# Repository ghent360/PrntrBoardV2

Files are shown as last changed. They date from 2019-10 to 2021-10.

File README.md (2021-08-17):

PrntrBoard V2
======================
PrntrBoard V2 is the next iteration of my 3D printer controller design. The V1 was very good, except it had one major drawback - the stepper drivers were soldered on the board which would make the design expensive.
This V2 design has 6 replaceable motor drivers. While traditional RAMPS based boards use pin headers to house the driver boards, I'm using PCIe 1x slots. This design has several advantages:
  + the driver PCB layout can be more flexible as there are fewer constraints on the driver board dimensions
  + drivers are placed vertically on the board which allows for more efficient space utilization as well as more efficient cooling
  + PCIe 1x slots have 36 pins which allows for greater design flexibility

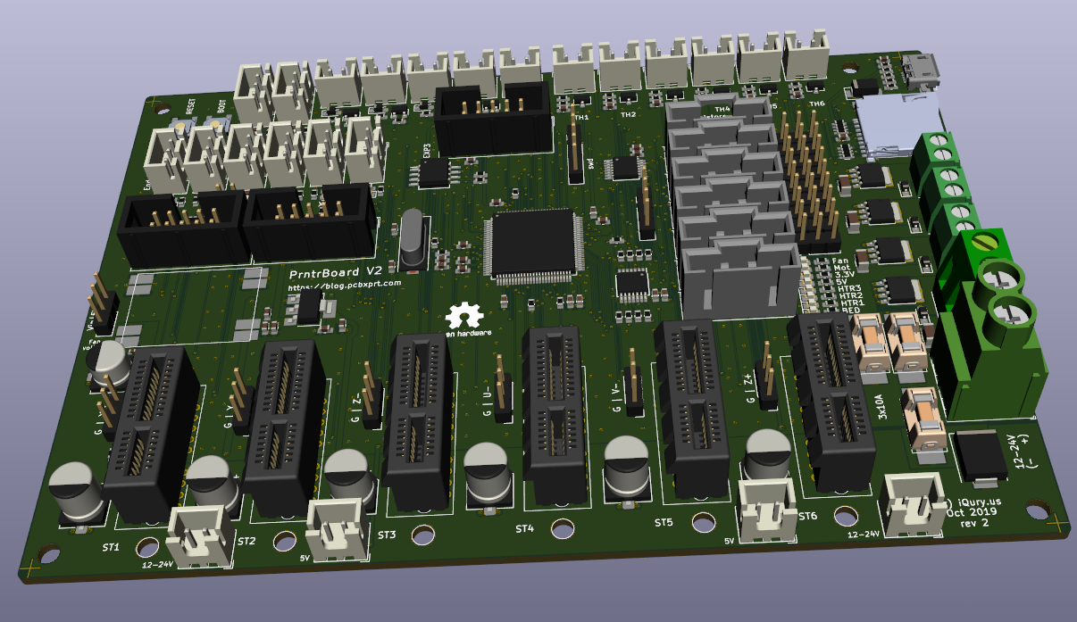
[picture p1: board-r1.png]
Picture of rev-1 KiCad Rendering


Project Status
-----
The following functionality has been verified on the rev1 prototype board with Marlin firmware:
  + TMC2660 and TMC2209 drivers working and able to move motors
  + Endstops
  + Heaters and thermistor inputs
  + LCD interface with 12864 panel from FYSETC and REPRAP Discount Graphics Panel.
  + Micro SD-card interface
  + EEPROM
  + Fan control

Features of the board:
-----
  + up to 6x replaceable stepper motor drivers
  + 32-bit Arm processor with floating point support running at 168MHz (STM32F407)
  + up to 6 thermistors or 6 thermocouples for temperature control
  + 4 power heaters (1 bed and up to 3 extruder heaters) with PWM power control
  + 5 low power PWM connectors with selectable voltage (5V vs 12-24V) for fans or LEDs
  + 8 end stops with option to use stall detection from the stepper drivers on 6 of them
  + micro-sd card support with SDIO for fast file transfer
  + 2 extra serial ports for WiFi and or smart LCD screen control
  + RAMPS LCD screen support
  + Marlin 2.0 firmware or Smoothieware V1.0, RRF port in progress, Klipper port in progress.
  + 4 extra fan connectors (2x5V and 2x12-24V)
  + Input voltage: 12-24V
  + CAN bus connector contributed by ArkadiuszRaj.

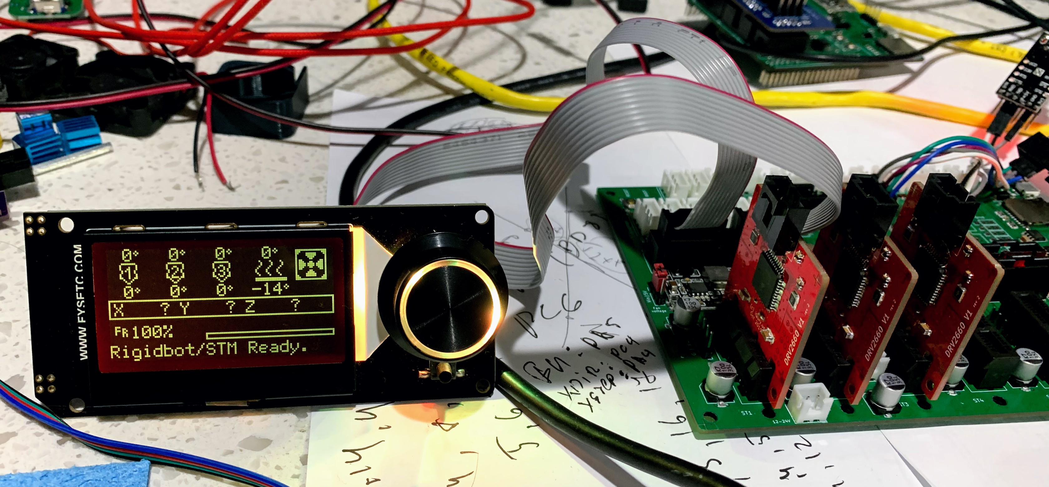
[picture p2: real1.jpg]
Picture of rev-1 prototype


Drivers
------
High power driver using Trinamic TMC2660. Should support up to 2.5A RMS current per phase with forced cooling. Supports stall detection. Driver current is adjustable via SPI.

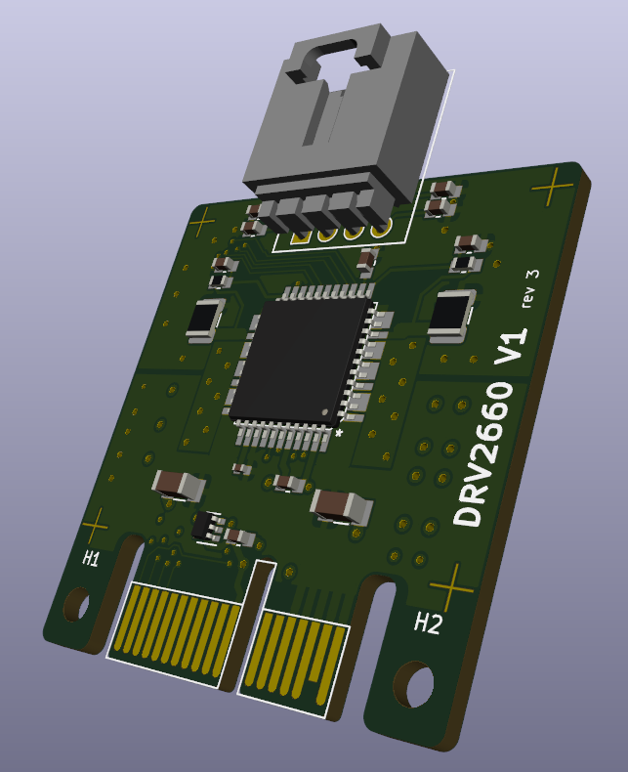
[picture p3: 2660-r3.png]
KiCad rendering of the 2660 driver board
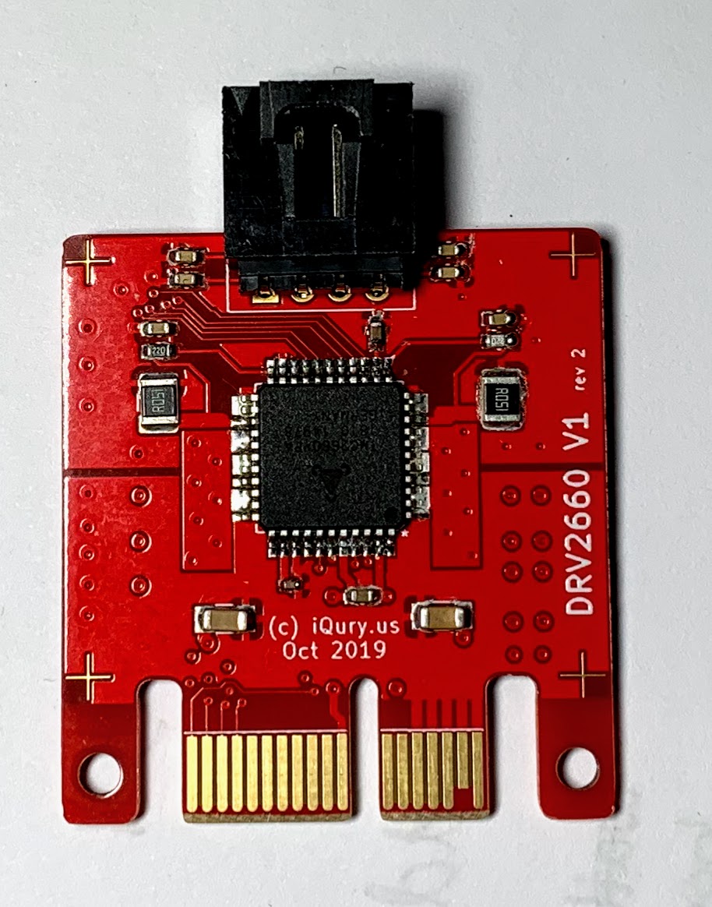
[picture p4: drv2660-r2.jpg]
2660 r2 driver board
 

Versatile "economy" driver using Trinamic TMC2209. Should support up to 1.8A RMS current per phase with forced cooling. Supports stall detection. Driver current is adjustable via UART.

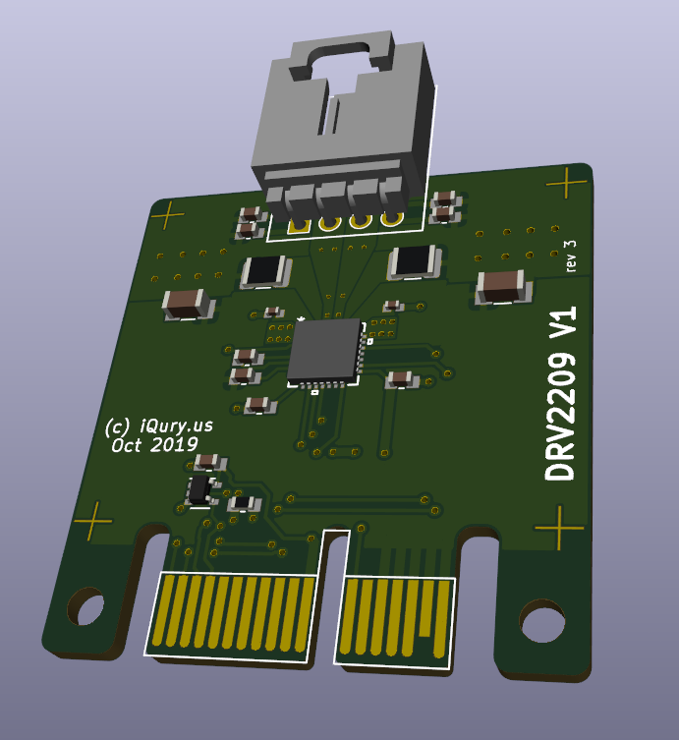
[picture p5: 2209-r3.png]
KiCad rendering of the 2209 driver board
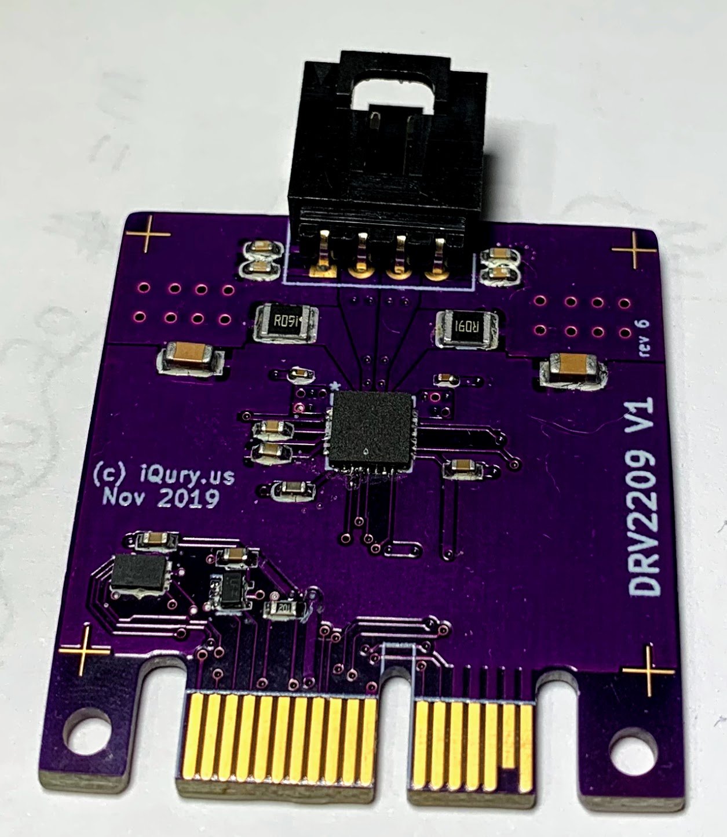
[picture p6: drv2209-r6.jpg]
2209 r6 driver board


High voltage driver (up to 42V) using Trinamic TMC2130. Should support up to 1.1A RMS current per phase with forced cooling. Supports stall detection. Driver current is adjustable via SPI. The driver board has separate power terminal.

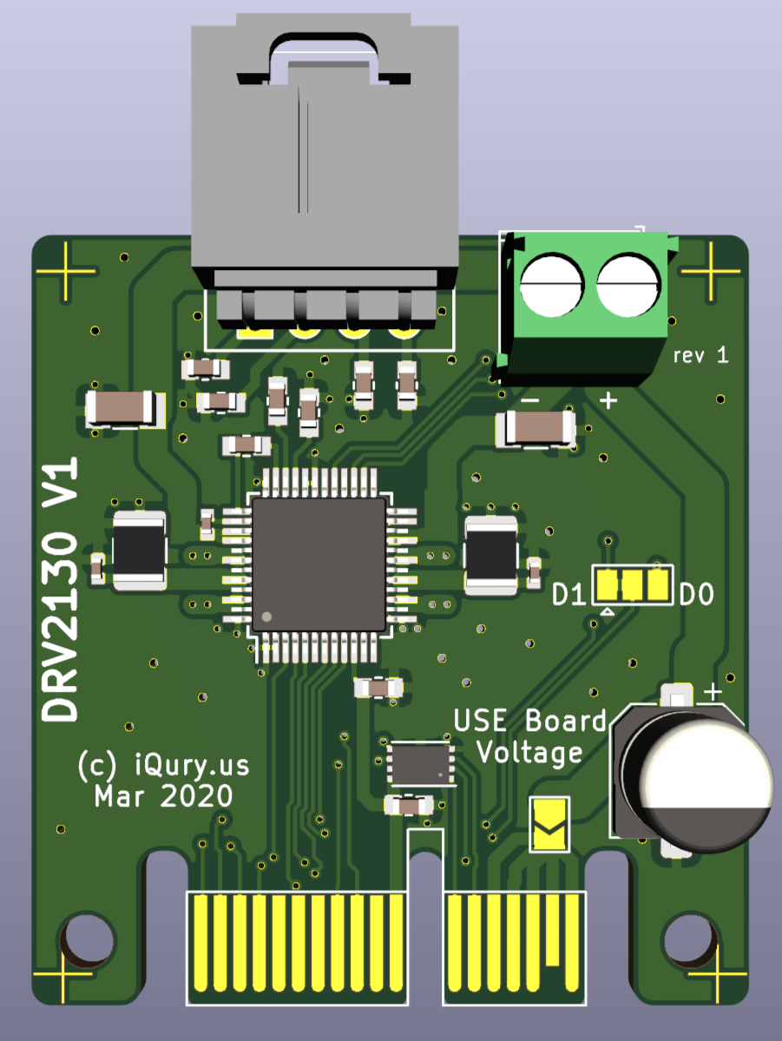
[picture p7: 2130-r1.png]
KiCad rendering of the 2130 driver board


Very high current driver design using TMC5161 and TMC2160 with external MOSFETS are also possible. In addition an adapter board for Pololu style stepper drivers is planned for backwards compatibility with old drivers.

Software
------

Marlin v2 is working on the board. I have a port of Smoothieware V1. Klipper is functional with some [fixes] (https://github.com/ghent360/klipper). RepRepFirmware ports is in early stages and not yet functional.

Visit [my blog](https://blog.pcbxprt.com/) for status updates on the development of the board.

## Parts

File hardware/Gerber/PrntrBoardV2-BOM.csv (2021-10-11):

Comment | Designator | Footprint | LCSC | LCSC Part # | Part #
10uF | C20,C23,C26,C56,C2,C5,C6,C15 | PrntrBoardV2:C_0603_1608Metric |  | C19702 | CL10A106KP8NNNC
0.1uF | C21,C22,C57,C18,C19,C54,C1,C4,C7,C8,C9,C10,C11,C12,C13,C14,C17,C53,C46 | PrntrBoardV2:C_0603_1608Metric |  | C14663 | CC0603KRX7R9BB104
0.1uF 50V | C24 | PrntrBoardV2:C_0603_1608Metric |  | C14663 | CL05B104KO5NNNCC0603KRX7R9BB104C
100uF 35V | C25,C47,C48,C49,C50,C51,C52 | Capacitor_SMD:CP_Elec_6.3x7.7 |  | C134792 | VES101M1VTR-0607
1000pF | C27,C28,C29,C30,C31,C32,C33,C34,C35,C36,C37,C38,C39,C40,C3,C16,C45 | PrntrBoardV2:C_0603_1608Metric |  | C1588 | CL10B102KB8NNNC
10uF 50V | C41,C42,C43,C44 | PrntrBoardV2:C_1206_3216Metric |  | C13585 | CL31A106KBHNNNE
B5819W | D1,D21,D22,D25,D26,D27,D29,D30,D31,D33 | Diode_SMD:D_SOD-123 |  | C8598 | B5819W
LED | D2,D3,D4,D5,D13,D14,D15,D16,D17,D18,D19,D20,D23,D24,D28,D32 | PrntrBoardV2:LED_0603_1608Metric |  | C2286 | KT-0603R
10V | D6 | Diode_SMD:D_SOD-323 |  | C131828 | LM3Z10VT1G
BAT54S | D7,D8,D9,D10,D11,D12 | Package_TO_SOT_SMD:SOT-23 |  | C181201 | BAT54S
IDC 2x5 | EXP1,EXP2,EXP3 | Connector_IDC:IDC-Header_2x05_P2.54mm_Vertical |  | C5661
500mA | F1 | PrntrBoardV2:R_0603_1608Metric |  | C261937 | TLC-FSMD050
Fuse | F2,F3,F4 | PrntrBoardV2:2410_FuseFolder
600 ohm @ 100MHz | FB1 | Inductor_SMD:L_0805_2012Metric |  | C1017 | GZ2012D601TF
JST XH | J1,J2,J22,J23,J24,J25,J26,J27,J_TH1,J_TH2,J_TH3,J_TH4,J_TH5,J_TH6,J4,J16,J18,J19,J21 | Connector_JST:JST_XH_B2B-XH-A_1x02_P2.50mm_Vertical
KF350 | J28,J6,J17,J20 | PrntrBoardV2:TerminalBlock_Phoenix_PT-1,5-2-3.5-H_1x02_P3.50mm_Horizontal
RJ12_Shielded | J29 | Connector_RJ:RJ12_Amphenol_54601
USB_B_Micro | J3 | PrntrBoardV2:MC-101C |  | C183609 | SOFNG MC-101C
KF129 | J5 | PrntrBoardV2:TerminalBlock_Phoenix_MKDS-1,5-2-5.08_1x02_P5.08mm_Horizontal
Conn_01x03_Male | J7,J8,J9,J10,J11,J12,J13,J14,J15 | Connector_PinHeader_2.54mm:PinHeader_1x03_P2.54mm_Vertical
Jumper_2_Open | JP1 | Connector_PinHeader_2.54mm:PinHeader_1x02_P2.54mm_Vertical |  | C160332
Jumper_3_Open | JP2,JP3,JP4,JP5,JP6,JP7,JP8 | Connector_PinHeader_2.54mm:PinHeader_1x03_P2.54mm_Vertical |  | C152153
Serial 0 | J_SER1 | Connector_PinHeader_2.54mm:PinHeader_1x04_P2.54mm_Vertical |  | C358686
PCIe_Stepper | J_ST1,J_ST2,J_ST3,J_ST4,J_ST5,J_ST6 | PrntrBoardV2:AMPHENOL_10018784-10210TLF
SWD | J_SWD1 | Connector_PinHeader_2.54mm:PinHeader_1x05_P2.54mm_Vertical
JST XH 3p | J_U-1,J_V-1,J_X+1,J_X-1,J_Y+1,J_Y-1,J_Z+1,J_Z-1 | Connector_JST:JST_XH_B3B-XH-A_1x03_P2.50mm_Vertical
KF635 | J_power_in1 | TerminalBlock_MetzConnect:TerminalBlock_MetzConnect_Type701_RT11L02HGLU_1x02_P6.35mm_Horizontal
Net-Tie_2 | NT1 | NetTie:NetTie-2_SMD_Pad0.5mm
NCE40P40K | Q1 | Package_TO_SOT_SMD:TO-252-2 |  | C130100 | NCE40P40K
22 | R10,R11,R72 | PrntrBoardV2:R_0603_1608Metric |  | C23345 | 0603WAF220JT5E
10k | R13,R14,R19,R20,R23,R24,R27,R28,R2,R73,R77,R78,R32,R33,R34,R38,R39,R40,R43,R44,R47,R1,R3,R5,R6,R7,R70,R48,R49,R50,R54,R55,R56,R58,R60,R61,R63,R64,R67,R68 | PrntrBoardV2:R_0603_1608Metric |  | C25804 | 0603WAF1002T5E
470 | R15,R45,R46 | PrntrBoardV2:R_0603_1608Metric |  | C23179 | 0603WAF4700T5E
1k | R16,R29,R30,R31,R35,R36,R37,R41,R42,R8,R51,R57,R62,R65,R69 | PrntrBoardV2:R_0603_1608Metric |  | C21190 | 0603WAF1001T5E
4k7 | R17,R18,R21,R22,R25,R26 | PrntrBoardV2:R_0603_1608Metric |  | C23162 | 0603WAF4701T5E
180 | R52,R53,R59,R66 | PrntrBoardV2:R_0603_1608Metric |  | C22828 | 0603WAF1800T5E
100k | R71,R12 | PrntrBoardV2:R_0603_1608Metric |  | C25803 | 0603WAF1003T5E
56 | R74,R75 | PrntrBoardV2:R_0603_1608Metric |  | C25196 | 0603WAF560JT5E
1.5k | R9 | PrntrBoardV2:R_0603_1608Metric |  | C22843 | 0603WAF1501T5E
4x470 | RN1,RN2 | Resistor_SMD:R_Array_Convex_4x0603 |  | C25510 | 4D03WGJ0471T5E
4x10k | RN3 | Resistor_SMD:R_Array_Convex_4x0603 |  | C29718 | 4D03WGJ0103T5E
SW_Push | SW_BOOT1,SW_RST1 | PrntrBoardV2:Button_4x4 |  | C318884 | TS-1187A-B-A-B
TC | TC1,TC2,TC3,TC4,TC5,TC6 | kicad-molex-sl-footprints:Molex-SL-6POS
SI2318CDS | TR1,TR4,TR6,TR7,TR9 | PrntrBoardV2:SOT-23 |  | C20917 | AO3400A
PSMN7R0-30YL | TR2,TR3,TR5,TR8 | PrntrBoardV2:SOT-669_LFPAK |  | C427523 | PSMN1R5-30YLC
74LVC125 | U1,U7 | Package_SO:TSSOP-14_4.4x5mm_P0.65mm |  | C6059 | 74LVC125APW,118
STM32F407VETx | U2 | Package_QFP:LQFP-100_14x14mm_P0.5mm |  | C28730 | STM32F407VET6
24LC64 | U3 | Package_SO:SO-8_3.9x4.9mm_P1.27mm |  | C5460 | 24LC64T-I/SN
AMS1117-3.3 | U4 | Package_TO_SOT_SMD:SOT-223-3_TabPin2 |  | C6186 | AMS1117-3.3
74HCT04 | U6 | Package_SO:TSSOP-14_4.4x5mm_P0.65mm |  | C131317 | 74HCT04PW,118
TJA1040 | U8 | Package_SO:SOIC-8_3.9x4.9mm_P1.27mm |  | C6951 | TJA1040T/CM,118
12MHz | X1 | Oscillator:Oscillator_SMD_EuroQuartz_XO32-4Pin_3.2x2.5mm |  | C29752 | SIT1602AI-22-33E-12.000000D
MicroSD | XS1 | PrntrBoardV2:Conn_uSDcard |  | C111196 | SOFNG TF-15×15

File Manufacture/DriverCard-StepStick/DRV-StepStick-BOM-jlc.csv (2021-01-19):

Comment | Designator | Footprint | LCSC | LCSC Part # | Part #
0.1uF | C3 | PrntrBoardV2:C_0603_1608Metric |  | C14663 | CC0603KRX7R9BB104
100uF 35V | C4 | Capacitor_SMD:CP_Elec_6.3x7.7 |  | C134792 | VES101M1VTR-0607
PCIe_Stepper | J1 | Connector_PCBEdge:BUS_PCIexpress
Motor | J2 | PrntrBoardV2:Molex-SL-4POS
StepStickL | J3 | Connector_PinSocket_2.54mm:PinSocket_1x08_P2.54mm_Vertical
StepStickR | J4 | Connector_PinSocket_2.54mm:PinSocket_1x08_P2.54mm_Vertical
Conn_01x04 | J5 | Connector_PinHeader_2.54mm:PinHeader_1x04_P2.54mm_Vertical
SPI Mode | J6 | Connector_PinHeader_2.54mm:PinHeader_2x04_P2.54mm_Vertical
Conn_01x02 | J7 | Connector_PinSocket_2.54mm:PinSocket_1x02_P2.54mm_Vertical
Clock/Sleep | JP3 | Connector_PinHeader_2.54mm:PinHeader_1x03_P2.54mm_Vertical
Reset | JP4 | Connector_PinHeader_2.54mm:PinHeader_1x03_P2.54mm_Vertical
10k | R1,R2 | Resistor_SMD:R_0603_1608Metric |  | C29718 | 4D03WGJ0103T5E
74LVC1G06 | U2 | Package_TO_SOT_SMD:SOT-353_SC-70-5 |  | C7828 | SN74LVC1G06DCKR

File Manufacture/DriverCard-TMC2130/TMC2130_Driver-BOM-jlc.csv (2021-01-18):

Comment | Designator | Footprint | LCSC | LCSC Part # | Part #
0.1uF | C1,C6,C16,C17 | PrntrBoardV2:C_0603_1608Metric |  | C14663 | CC0603KRX7R9BB104
1000pF | C11,C12,C13,C14 | PrntrBoardV2:C_0603_1608Metric |  | C1588 | CL10B102KB8NNNC
10uF 50V | C2,C4 | PrntrBoardV2:C_1206_3216Metric |  | C13585 | CL31A106KBHNNNE
0.022uF 50V | C3 | PrntrBoardV2:C_0603_1608Metric |  | C21122 | CL10B223KB8NNNC
100uV 35V | C5 | Capacitor_SMD:CP_Elec_6.3x7.7 |  | C171732 | VE-101M1VTR-0607
4.7uF | C7 | PrntrBoardV2:C_0603_1608Metric |  | C19666 | CL10A475KO8NNNC
0.47uF | C8 | Capacitor_SMD:C_0603_1608Metric |  | C1623 | CL10B474KA8NNNC
0.1uF 50V | C9,C10,C15 | PrntrBoardV2:C_0402_1005Metric |  | C1525 | CL05B104KO5NNNC
SBRT5A50SA | D1 | Diode_SMD:D_SMA |  | C264107 | SBRT5A50SA-13
3A | F1 | Fuse:Fuse_1206_3216Metric |  | C208499 | SF-1206F300-2
PCIe_Stepper | J1 | Connector_PCBEdge:BUS_PCIexpress
Conn_01x04_Male | J2 | PrntrBoardV2:Molex-SL-4POS
Screw_Terminal_01x02 | J3 | TerminalBlock_Phoenix:TerminalBlock_Phoenix_PT-1,5-2-3.5-H_1x02_P3.50mm_Horizontal
DIAG_Sel | JP1 | Jumper:SolderJumper-3_P1.3mm_Bridged12_Pad1.0x1.5mm
Use VM | JP2 | Jumper:SolderJumper-2_P1.3mm_Open_TrianglePad1.0x1.5mm
0R12 | R1,R2 | Resistor_SMD:R_2512_6332Metric |  | C81248 | 25121WF120LT4E
TMC2130 | U1 | PrntrBoardV2:tmc5130-nc |  | C328952 | TMC2130A-TA
24LC02 | U2 | PrntrBoardV2:TDFN-8-1EP_3x2mm_P0.5mm_EP1.56x1.45mm |  | C184154 | CAT24C02VP2IGT3A

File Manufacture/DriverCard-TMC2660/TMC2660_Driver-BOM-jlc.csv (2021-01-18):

Comment | Designator | Footprint | LCSC | LCSC Part # | Part #
10uF 50V | C1,C2 | PrntrBoardV2:C_1206_3216Metric |  | C13585 | CL31A106KBHNNNE
100uF 35V | C13 | Capacitor_SMD:CP_Elec_6.3x7.7 |  | C171732 | VE-101M1VTR-0607
0.1uF | C3,C6,C14 | PrntrBoardV2:C_0603_1608Metric |  | C14663 | CC0603KRX7R9BB104
0.1uF 50V | C4 | PrntrBoardV2:C_0402_1005Metric |  | C1525 | CL05B104KO5NNNC
0.47uF | C5 | PrntrBoardV2:C_0603_1608Metric |  | C1623 | CL10B474KA8NNNC
0.01uF | C7,C12 | PrntrBoardV2:C_0603_1608Metric |  | C57112 | 0603B103K500NT
1000pF | C8,C9,C10,C11 | PrntrBoardV2:C_0603_1608Metric |  | C1588 | CL10B102KB8NNNC
PCIe_Stepper | J1 | Connector_PCBEdge:BUS_PCIexpress
Conn_01x04_Male | J2 | PrntrBoardV2:Molex-SL-4POS
22R | R1,R3 | PrntrBoardV2:R_0603_1608Metric |  | C23345 | 0603WAF220JT5E
0R051 | R2,R4 | Resistor_SMD:R_2512_6332Metric |  | C270949 | CS121WF510MT4E
TMC2660 | U1 | PrntrBoardV2:TMC2660 |  | C92654 | TMC2660-PA
74LVC1G06 | U2 | Package_TO_SOT_SMD:SOT-353_SC-70-5 |  | C7828 | SN74LVC1G06DCKR
24LC02 | U3 | PrntrBoardV2:TDFN-8-1EP_3x2mm_P0.5mm_EP1.56x1.45mm |  | C184154 | CAT24C02VP2IGT3A

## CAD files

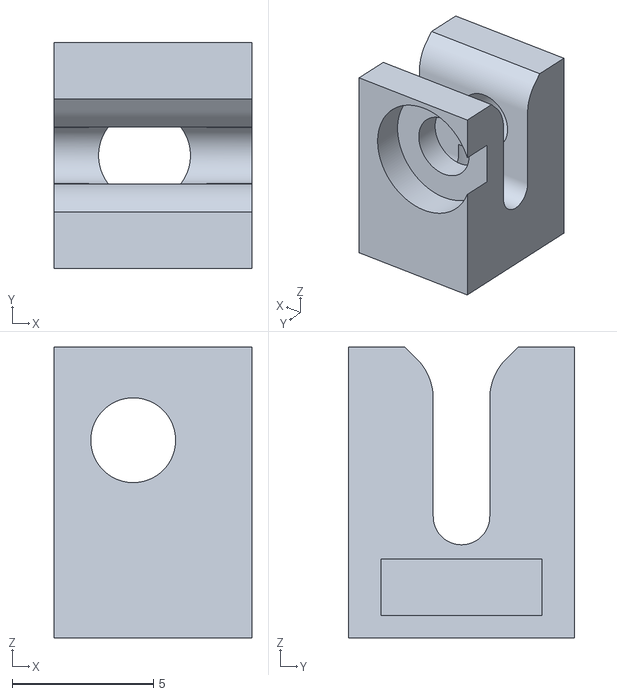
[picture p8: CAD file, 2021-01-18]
Manufacture/STL/DriverMount.stl
7.00 x 8.00 x 10.3

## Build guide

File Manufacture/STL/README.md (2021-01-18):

# Instructions how to mount the driver boards

materials needed (per driver board):
* M3 button head screw 5mm - 4pcs
* M3 square flat nut - 2pcs
* M3 insulating washer - 2pcs - nylon of fyber
* DriverMount 3D printed - 2pcs
* Front heat sink - 14x14x8mm or 14x14x6mm or 14x14x7mm.
* Back heat sink - 25x25x5mm

Mount the heat sinks to the board. Make sure the back heat sink is centered and does not short the motor connector pins. The front heat sink should also be somewhat centered on the chip. The fins on the front and back heat sink should be horizontal, not vertical.

Attach the mount feet to the driver board on both sides using M3 screws - not not tighten completely the feet should be able to rotate with minimal force. The mount holes on the driver board are smaller so the screw would be a tight fit and there is no need for a nut. Make sure the hole for the square nut is on the outside of the driver board, not facing the PCIe slot.

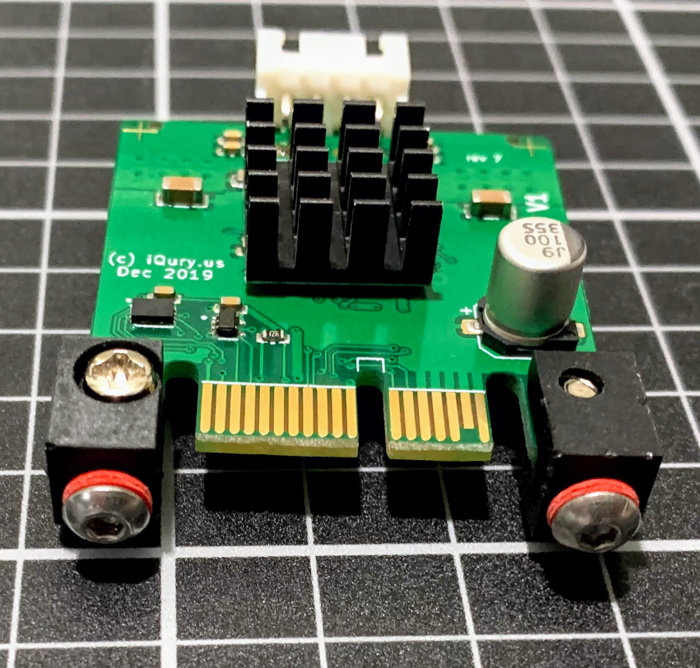
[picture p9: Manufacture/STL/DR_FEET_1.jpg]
Driver foot mounted


Insert the square M3 nuts in the opening on the bottom of each mount foot.

Insert the driver into the PCIe slot on the board. Attach the driver with 2 M3 screws on the bottom of the board and use the insulating washers to prevent the screw from damaging the board.

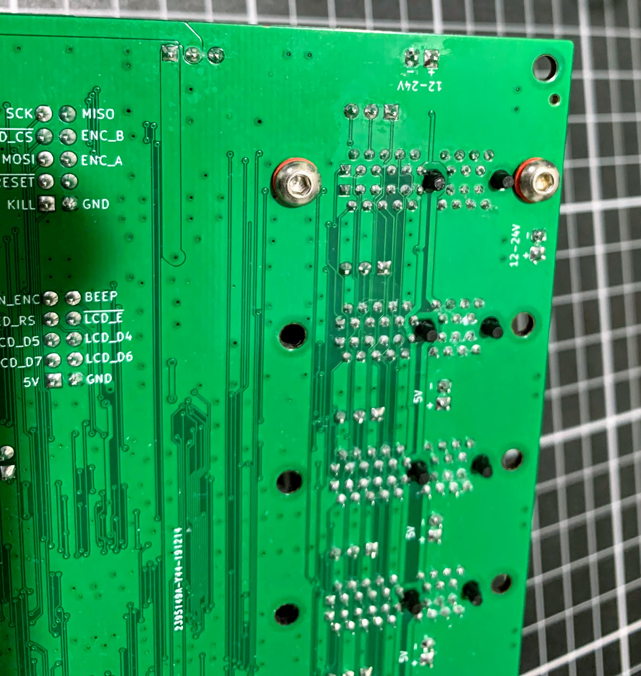
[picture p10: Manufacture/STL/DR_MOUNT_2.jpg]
Bottom mount screws


Repeat for the other driver boards

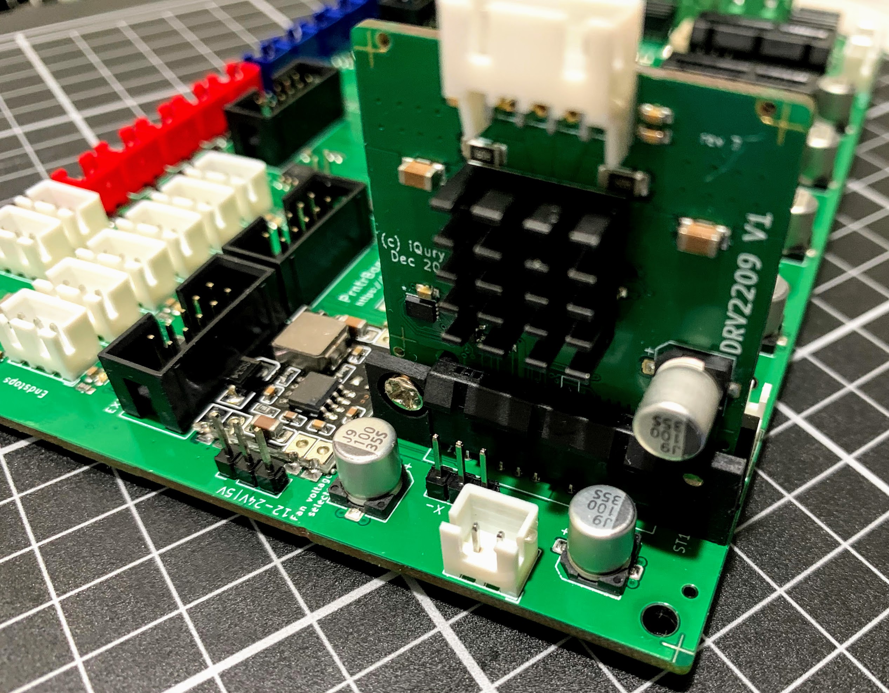
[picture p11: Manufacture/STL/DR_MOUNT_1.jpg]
Board mounted


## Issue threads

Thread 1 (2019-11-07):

Schematic library missing

cruse123, 2019-11-07:
Symbols in schematics cannot be normally displayed, showing rectangles with question marks. When double-clicking the part and the icon button at "Symbol - Library Reference", an error message prompts saying `Library file '.....\PrntrBoardV2\hardware\10018784-10210TLF.lib' not found. Use the Manage Symbol Libraries dialog to fix the path (or remove the library).` Maybe there should be a library file named "10018784-10210TLF.lib" but not uploaded to the repository?

Screenshots are as follows:

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

Many thanks!

ghent360, 2019-11-07:
Thank you for reporting the issue with the schematics. I'll take a look and try to improve the content of the repo, so it is self contained.

As far as "10018784-10210TLF.lib" - it is not needed and while there is a warning on my system as well. I'm able to see the schematics, so that is not what is causing the problem for you.

It is very inconsiderate of me to leave a broken library reference in the sym-lib-table. I'll remove it asap.

ghent360, 2019-11-08:
Hello, would you kindly let me know, what version of KiCad are you using?
I tried to download the project on a different computer and I was able to view the schematics with no issues with version 5.1.4 (latest stable build). Unfortunately that version was unable to display the PCB, for that you need the nightly development branch.

I did verify that after installing the build from today (11/7/2019) I was able to view both the schematics as well as the PCB.

For convenience I added a PDF of the schematics in the hardware/doc folder.

cruse123, 2019-11-08:
Hello!
After pulling the new commits, schematic symbols can be normally displayed, without any errors at all! I was using the latest stable release `kicad-5.1.4_1` at that time and everything in schematics went well. Problems solved. Thanks a lot!

However, as you have mentioned, PCB layout document cannot be opened in this "lower" version. Switching to today's latest nightly build `kicad-r14425.6182133a4` works. If a stable version is preferred, manually modifying the `kicad_pcb` document may help: Expand error information in the kicad dialog, delete the "Unexpected" lines in the PCB document with text editors. This may be an imperfect solution, so for read-only previewing only.  Using the proper version for further editing / manufacturing is recommended in my opinion.

Thanks again!

Closed 2019-11-09.

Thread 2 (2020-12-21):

when trying to open pcb file it says date of kicad version required is newer after 19 jan 2020

svalambhia, 2020-12-21:
I am using kicad 5.1.8 nov 2020 but still when open pcb file i got error   kicad version required is newer after 19 jan 2020. schematic works fine. I remember I had open pcb file in older kicad version.
i tried to download new files for github and tried to open it ... it gives same error. do I need to go back to old version ?

ghent360, 2020-12-21:
I’m using KiCad 6 nightly builds.

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

svalambhia, 2020-12-21:
Oh ok

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

Closed 2021-01-14.

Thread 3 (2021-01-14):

RRF compatibility

ArkadiuszRaj, 2021-01-14:
Hello,

First of all congrats for this work.
As a foreword I want to express my openness in helping porting of the STM RRF to support this board. I am interested in assembling of this board for my purposes but to do so (make RRF running) I think small modifications are necessary.

- enable CAN to allow using Duet3 modules. This can be done by small remapping of GPIO (PD0-1 for CAN, move ST5/6_STEP to PE7-8 and combine U_MIN/Z_MAX inputs with SWDIO/SWCLK lines)
- resign from EXP1/EXP2 in favor of 4-pin TFT screen connection (like PanelDue) as I think those EXPs are ancient interface nowadays:)
- add Wi-Fi by mimicking available adapters of NodeMCU/esp8266

I plan to use your design in future to control my Voron2.4 printer, which uses 6 motors to drive 3 axes. Thus I will need CAN to talk to Duet3 1LC for hotend. That is simpler than supporting 8x PCIe slots.

Why DC converter module is not vertically installed using something like 2.54 2x4 headers? Can you share background of this decision to place it horizontally?

I also think adding second converter in parallel, converting VIN to 12V to allow selection of this voltage to drive fans - much much cheaper fans as broadly available on computer market.

BTW, have you verified PCB with STM32F7 cpu?

Appreciate your comments.

Regards

Arkadiusz

ghent360, 2021-01-14:
Hi Arkadiusz,

I'll think about adding CAN interface, thank you for the suggestions. There is a spare SPI and serial and I2C interfaces on EXP3 port. Between these and the EXP1/EXP2 GPIOs it should be possible to connect serial TFT display and Wi-Fi module.

The boost converter module I use has castellated edges and solders onto the board very easily (https://www.aliexpress.com/item/32713451014.html?spm=a2g0s.9042311.0.0.27424c4dCd0jRT). I found that the cost of this module is less than the cost of parts I would need to add one to the board. You can add external 12V regulator and feed the 12V info the middle of the fan voltage selector pin. This would make the fans work at 12V. The MOSFETS are rated for up to 40V, so I would not go higher than 30V on that pin.

I have not considered the F7 chips, because they are much more expensive and I don't think the existing software utilizes the F4 to the level that would justify the cost increase. I did make a version with an H750, chip (new_cpu branch). That however needs a more complex bootloader as the chip does not have enough flash to store the firmware and it needs to be loaded from SPI flash or sd-card into RAM.

I do use the JLCPCB assembly service to order partially populated board. The KiCAD file has all component references for the JPC part numbers that are needed. The boards come without the micro-sd card connector, no micro usb connector and no DC buck converter. You would also need to solder all true hole connectors you care about. It takes me about an hour to assemble one board. The JLC service has a limit on the variation of components one can place on the board, which is one more reason to skip on the DC converter and use premade one.

Happy to chat more.

ArkadiuszRaj, 2021-01-14:
Hello

Yes I saw this specific branch regarding H7 series chip. My mistake with
wrong character:)

I have already updated schematic with CAN interface, not yet on pcb though.
Will share image later on.

Also while using JLCPCB I would swap 0603 into 0402 to save some space.
However keeping 2 layer design from one hand make manufacturing them
cheaper but is much more challenging from routing perspective. Must admit
that for some time I am using JLCPCB for 4-layer PCBA but with PCB not
exceeding 10x10cm.

So changing to 0402 and some cleaning up of tracks. That is the way forward
to my understanding.
Also when it will be possible to cut some mm from both dimensions this
design can jump into 4 layers and compact size even more.

Wi-Fi is the least problematic addon.

W dniu czw., 14.01.2021 o 17:55 ghent360 <notifications@github.com>
napisał(a):

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

ArkadiuszRaj, 2021-01-14:
As promised, CAN interface  as simple as possible:
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
and gpio remapping...
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

Actually diodes connecting U_MIN/Z_MAX with SW lines are to me not necessary as I presume SWD port is used only for initial flashing or possibly never at all.

BTW, with 0402 there is possibility to fit some resistors/diodes that I saw outside the board (full_prot branch):

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
this is excerpt of the PCB close to J12...

and  BAT54S...
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

ghent360, 2021-01-14:
Most of the board size is dictated by the external connectors. 10x10cm would be very challenging. My V1 design was using that, but the layout of the connectors was very impractical.

ghent360, 2021-01-15:
FYI the extClock is the most up-to-date branch.

I have another idea for scrounging a few extra pins: the sdio can work in 1-bit mode, so we can re-task the SDIO_D2, D3 and D4 pins. As a practical matter it is not stable in 4-bit mode with the current layout anyway - I suspect the signal return path is quite bad with only 2 layers.

ArkadiuszRaj, 2021-01-15:
Hi

Thanks for pointing proper branch for changes. Actually this is something I wanted to ask you.

Referring the connector placement and board ergonomics I agree. I even think one can scarify additional few euros to have 4 layer board (8 vs 32). This way the pcb can have better power distribution and shielding characteristics. Yet 4-layers can be treated as roadmap item. Now the important part is CAN to me.

I will then update schematic on the pointed branch and create PR.

For the board itself as for now I will only do cleanup of the tracks what shall make life easier when change to 0402 happen.

ghent360, 2021-01-15:
Do you want to place the can i/o on the board or as add-on via header?

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

ghent360, 2021-01-15:
Btw I want to remove the connector next to the micro-sd card. It does not
serve any useful purpose.

On Fri, Jan 15, 2021 at 12:54 AM Venelin Efremov <veffremov.ve@gmail.com>
wrote:

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

ArkadiuszRaj, 2021-01-15:
Hi,

1) WiFi using add-on board and utilizing EXP1/EXP2, simimalar to SKR RRF WiFi, but in a shape of [SKR GTR adapter ](https://www.tindie.com/products/pcr/reprapfirmware-wifi-adapterboard-for-gtr/)

2) CAN - albeit I prefer integration it can also be an add-on. But in this case a PCB must be modified to release CPU pins dedicated to CAN interface.

3) I did a clean up of the tracks and added 5V terminal to use for installations, where external power supply is controled by board, i.e. cut off of the VIN is controlled by gcode. BTW I think I saw somewhere in branches PSU output, or am I mistaken?
Anyway this is how it looks, I had to reorder overvoltage protection components.
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

4) You want to remove EXT4? Which as I understand exposes the SDIO lines?
Yes, current routing is not good for high speed communication. This means it realy can be tailored down do simple SPI card access. Frankly speaking, in such a control boards there is no need for high speed communication.

ghent360, 2021-01-15:
Any thoughts on using TJA1040? Allegedly you can skip the common mode choke.

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

ArkadiuszRaj, 2021-01-16:
Please find corrections in PR https://github.com/ghent360/PrntrBoardV2/pull/4

ghent360, 2021-01-16:
Merged.

Closed 2021-01-16.

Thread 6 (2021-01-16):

WiFi Addon

ArkadiuszRaj, 2021-01-16:
PR already provided #7

ESP-12F used, to allow usage of DWC. Connected to main board via SPI2 exposed on EXT1/2 ports
Local USB to easly update firmware of the ESP.
As EXT1/2 do not provide 3V3 I have put also local dc-dcconverter.

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

ArkadiuszRaj, 2021-01-16:
If stacking for legacy LCD would be needed I sugegst to use long led 5x2 header sockets

ArkadiuszRaj, 2021-01-17:
Correction to Header placement and spacing applied. Sorry for missing checking such a basic stuff

ArkadiuszRaj, 2021-01-17:
Regarding RST - it is essential and shall be connected.

My bad I have not checked the EXP ports.

ghent360, 2021-01-17:
Well, not your fault. I just noticed it by chance when trying to see if the
connector of the addon lines up with the connector on the board. Again
thank you for the effort.

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

ghent360, 2021-01-17:
I think this PR is done and we can close it. We can fix the EXP2.4 pin in the main board schematics as separate issue.

Closed 2021-01-17.

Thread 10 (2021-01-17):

sd-card i/o rework & fix

ghent360, 2021-01-17:
At the moment the sd-card connector is broken (missing CS pin connection).
We can:

1. Move the sd-card to use hardware SPI1, freeing the SPI3 pins.
2. Scrounge some new pin for the CS connection
3. Switch the sd-card back to 1 bit SDIO and scrounge for pins.

Downside of #1 and #2 is that I need new bootloader to read sd-card via SPI. Not a terribly big issue.
Downside for #2 and #3 is that we are short on pins again &^%@#$%^!

Best to probably byte the bullet on the bootloader and do #1, we'll have a few extra IO pins, which is nice.

ArkadiuszRaj, 2021-01-18:
Vote for option 1, i.e move sd card tp spi1.

Also Iam interested in paricipating in IAP bootloader development.
But to do so, I need first a board itself. However I want to await this as well as #9 issue is solved.

ghent360, 2021-01-18:
Code for the bootloader:
https://github.com/ghent360/STM32F4_Bootloader

ghent360, 2021-01-18:
Re-wired the SD-card to SPI1 in the schematics and added extra pins to EXP2 and EXP3. Removed 3.3V from EXP3.

Need to route the changes in the PCB.

ghent360, 2021-01-18:
It has been routed. Thank you @ArkadiuszRaj

Closed 2021-01-18.

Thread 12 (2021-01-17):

StepStick driver considerations

ArkadiuszRaj, 2021-01-17:
Did another small thing, found inside PR #11

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

Questions:
- shall DIAG output of the stepstick (TMC one) be connected to Alarm1?
- what is purpose of CFG1-3 pins on the PCI slot? i.e PrntrBoard do not use them.
- what is the purpose of this small eeprom on drive board?

ArkadiuszRaj, 2021-01-18:
I saw your schematic changes and as I have some spare time I have played a bit with routing.

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

4 layers, one used to distribute V_IO.

That is preliminary view. I have added more vias around cap ground.

ghent360, 2021-01-18:
I added one more jumper and routed it in 2 layers. May need some more vias
for the GND. Add your handle to the Copyright, it is mostly your design.

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

ArkadiuszRaj, 2021-01-18:
PR #13 ready

ghent360, 2021-01-18:
Merged.

Closed 2021-01-18.

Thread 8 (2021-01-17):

Folders structure enhancement

ArkadiuszRaj, 2021-01-17:
I suggest to add following folder structure
- (one folder per product)

  - Manufacture

    - schematics.pdf
    - ibom.html
    - gerbers.zip
    - bom.csv
    - placement.csv

This is complete data for the ordering boards as well as assembly. Such a product manufacture' subfolder then represents "release" data content. If you agree I can start with making order following this suggestion.

ghent360, 2021-01-17:
The "Manufacture" folder sounds like a great idea. Since there are multiple
boards in this depot, we have to decide how to proceed:
Option 1) have board prefix: prntrboard_v2_schematics.pdf,
prntrboard_v2_ibom.htmletc for the main board; then tmc2209_schematics.pdf
tmc2209_ibom.html etc.
Option 2) have subfolders: Manufacture\prntrboardv2; Manufacture\tmc2209
etc.

I personally favor #2 since with #1 the list of files would be quite large
and hard to manage what is what, but I'm open to other suggestions.

~V

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

ArkadiuszRaj, 2021-01-17:
Option #2 follows my idea.

I will refactor files but will not add jlcpcb assembly files. Have no idea
how you create those and frankly speaking it is painful process as they do
not follow any standard of initial orientation. Thus every project one must
check if components orientation is OK.

W dniu niedz., 17.01.2021 o 17:02 ghent360 <notifications@github.com>
napisał(a):

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

ghent360, 2021-01-17:
I have a magic awk script that fixes the orientation on components I know
are wrong. JLC people are nice and will fix wrong orientation for you even
if you get it wrong, just have some cues in the silkscreen about the
correct orientation.

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

ghent360, 2021-01-17:
Yes I agree one has to check the orientation. Ill add the manufacture files
I have used and know to work well.

On Sun, Jan 17, 2021 at 8:28 AM Venelin Efremov <veffremov.ve@gmail.com>
wrote:

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

ArkadiuszRaj, 2021-01-17:
PR pushed, now the ball is yours 👍

What I am thinking about is that new version of for example TMC2209 driver shall not appear as additional file set but the repository shall by flagged with tags. Then information about revision in README file shall be updated keeping old data untouched.

ghent360, 2021-01-18:
I changed the StepStick driver schematics a bit. Removed the external voltage source - I'm not aware of any drivers that can be driven with over 24V successfully. Added local filter cap and a few jumpers to account for a variety of BTT and other drivers.

ghent360, 2021-01-19:
I updated all the driver boards.

Closed 2021-01-19.

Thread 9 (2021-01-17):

Fix EXP2 pin 4

ghent360, 2021-01-17:
EXP2 pin 4 is currently not connected. With the recent addition of the CAN interface we have spare GPIO pins and we can add a connection for that pin.

This pin is needed for the WiFi add-on board.

ArkadiuszRaj, 2021-01-18:
You have written:
"In the "reprap" screens that pin is usually used to detect if SD-card is inserted in the LCD sd-card slot. This is optional feature that I skipped because I was running out of pins."

~SD_DETECT is now connected to EXP2.7 which is connected to SD card switch and then to PD3 port.
So it is not a signal from the LCD screen own SD card. If one will use such a screen you think mixing of two SD_DETECTs is OK?

RRF Config tool for SKR1.4 produces
```
//ESP Settings
8266wifi.espDataReadyPin = 0.28;
8266wifi.lpcTfrReadyPin = 1.30;
8266wifi.espResetPin = 1.31;
//ESP RX/TX Settings
8266wifi.serialRxTxPins = { 4.29, 4.28 } ;
```
for GTR
```
//ESP Settings
8266wifi.espDataReadyPin = A.15;
8266wifi.lpcTfrReadyPin = C.11;
8266wifi.espResetPin = B.10;
//ESP RX/TX Settings
8266wifi.serialRxTxPins = { PC7, PC6 } ;
```
"ESP RX/TX Settings " is used solely for ESP firmware upgrade.

Anyway, for reset pin.

For SKR 1.4 - 1.31 is GPIO line connected to EXP2.4
For SKR GTR - B.10 same CPU as here, connected as well to EXP2.4, on schematics called EXP_SW_B10.

EXP SD_DETECT handling.

For SKR 1.4, EXP2.7 is connected directly to SSEL0 port of LPC
For SKR GTR, EXP2.7 it is EXP_SS_PB12 signal

TF card SD_DETECT:

For SKR 1.4 it is P0.27 line
For SKR GTR is is TF_SW connected to PC4

So as you can see, EXP SD_DETECT is different than "TF_DETECT".

Then I suggest:
- Left PD3 for internal SD_DETECT
- Assign PD2 for EXP_SW_RST (pin EXP2.4)
- Reuse two SWD pins as GPIO, this requires high imp buffer to not mix SWD with GPIO externally (or to make SWD functional)
- Use one of the SWD pins for connecting EXP2.7 (EXP_SD_DETECT)
- And still have one SWD/GPIO pin as buffer

ghent360, 2021-01-18:
Will be taken care of with issue #10 .

Closed 2021-01-18.

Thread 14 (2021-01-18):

StepStick better air flow

ghent360, 2021-01-18:
The distance between driver boards mounted vertically is 20mm. With the StepStick adapter, this does not leave a lot of room for heat sink on top of the driver. In addition on the bottom there is a wall of jumpers used for SPI/CFG switching, which would prevent air flow and installing heat sink on the bottom.

We should consider moving the SPI/CFG jumpers out of the way. Not a trivial task because there is not a whole lot of real estate left on the board. This will also break how these are traditionally organize on RAMPS boards and will require extra documentation.

ArkadiuszRaj, 2021-01-18:
Well, I think there can be space for moving out this pin forest.

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

But... I have doubts, as this will only fix for those , that have IC mounted on the bottom side. But majority of the older polulu drivers have chips on top side. Here, to make space for regular heatsink, maybe one can you low profile pin sockets? like these one https://www.aliexpress.com/item/622209657.html

ghent360, 2021-01-19:
Done.

Closed 2021-01-19.

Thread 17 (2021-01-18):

PCB review

ArkadiuszRaj, 2021-01-18:
After applying #10 I think it is a highest time for board review.
- proper track widths and clearances
- proper via sizes and clearances
- via to pad minimal distances for low connection impedance
- and so on...

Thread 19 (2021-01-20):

Some thought about usability, installation, ergonomics

ArkadiuszRaj, 2021-01-20:
Albeit the height of the driver card is relatively small the issue to me is the how to bend cables vertically.
So I came with idea to rotate the driver, exposing motor port to the right side. Why? as on this side there are motror supply voltage pins.

This way the cables came from the side, easier for installation and tying them.
As for start, I did checking the most complicated (to me) circuit, ie. 2130. nd that is how it looks.

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

No components bodies rendered as I wanted to show you how the power tracke look like.

ghent360, 2021-01-20:
One issue with this approach is the airflow. The drivers are designed for horizontal airflow like this:
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

The connectors would block the air path.

ArkadiuszRaj, 2021-01-21:
Fair enought.
My proposal comes from the idea of mounting single fanon top of teh enclousere, over the the board with cards. Larger one, like 80x80x15 to make it quiet.

BTW. Any reason to have such a strong air flow? Typical stepsticks with 2209 works fine with small heatsink and one single fan far away from them.

ghent360, 2021-01-22:
You can make an alternate PCB layout. I don't know how to have 2 PCBs on a single schematics, but it should be possible.

ArkadiuszRaj, 2021-01-22:
Actually started working on that. Some big reconstruction.

Assumption:
- 8 DRV cards,
- limit board size, to fit into cheap 6 layer PCB

Thus I did a spit of the controller board into two parts:
1- main with all connectors but the PCIex slots, to minimize size I put SMD components on back side, added DCDC buck converter using TDS5430, but.. .thinink about replacing cpu with 144 pin version, as...
2- PCI slots carrier, with 8 slots
Both are to be connected using 50 pin IDC ribbon cable.

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

Status:
- Carrier board routing completed, but I am still thinking into removal of screw terminal and pass the V_motors through several IDC pins. Board sIze is 95x80
-  Controller part: componnets placement alomst finished, power routing completed, some other as wel but stil hudrets of tracks to place.  Board sIze is 100x86

So as for now I am using orginal sub schematics, thus only 6 PCI will be used.
When completed and concept confrimed, I will start to reorganize the main board to use stm32f427 variance. More power, but also 8 PCIex. To do so, I will need to remove EXP1/2 connectors, leave only TFT for screen conenction and integrate the ESP-12 module directly on board. Quite a challanging but I like challanges :)

ghent360, 2021-01-22:
I would recommend against carrying large current over IDC cable. The power
input on the motor driver boar would allow the drivers to be run at 36V -
for example.

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

ArkadiuszRaj, 2021-01-22:
Yeah.

W dniu pt., 22.01.2021 o 18:34 ghent360 <notifications@github.com>
napisał(a):

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

ArkadiuszRaj, 2021-01-25:
So I have put 144 pin STM32F429 chip.

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

Routing is not completed, as I had to remap almost all signalling pins. I would say I am in teh miidle of teh way, having almost completed routing of those pins that uses STM32 peripherials, so general GPIO ones are left.
But during working on that following questions arise:

1) The ST_ALARM signals from different boards can be mapped to particluar endstop. But what is the reason for ALARM1 input? How FW shall handle that?
2) Purpose of the CLOCK dignal towards the driver cards, what is a gain if TMC uses internal or external clock?
3) Any reason to use 74HCT04 to drive Mosfets if Vds = 1.7V?

ArkadiuszRaj, 2021-01-25:
Also please notice the RJ footprint & 3d model.
I will push changes towards main branch with proper footprint for Wurth socket and make the decoupling R&C no more optional.

ghent360, 2021-01-25:
ST_ALARM was supposed to be a single line where all steppers can signal a stall (or other alarm condition) and the SF would interrogate each driver to determine the cause. This is all well in theory, but in practice Marlin does not support this (AFAIK).

TMC2130 drivers do not work for me without supplying a CLOCK signal. I'm not sure what the cause of this is the datasheet states they should be able to work with internal clock, but alas that is not the case. This was also an issue with PrntrBoardV1 with TMC2130 drivers. I don't know if this is only related to the tqfp package version, because the StepSticks which use the qfn package seem to work fine.

Not sure I understand Q3, the HCT04 is used to boost the gate drive voltage to ~5V so power mosfets can fully open. It would be even better is one can boost is to ~7V, but that would require separate power line or charge pump. Where is the Vds = 1.7V coming from?

ghent360, 2021-01-25:
Consider the STM32F427ZGT6 part, it is much cheaper than the 429.

ArkadiuszRaj, 2021-01-25:
ALARM1 - as far as I know Marlin/Klipper/RRF do not use that in TMC handling. Also printer boards I took a look at, maps ST_ALARM to ENDSTOP. So I take that as "good to have".

TMC2130 is old chip and for new designs I prefer 2209 / 5160. For legacy use... understand. Good to have CLOCK on DRV interface. Again, what is purpose of this small eeprom there?

Pricing. Be aware 429 is considered basic part, so from one hand is more expensive, but from other is almost the same price that 427 costs, which in turn is extended part.

Vds=1.7V? Taken a look at that spec https://docs.rs-online.com/7feb/0900766b812e05cf.pdf From fig 8 I can read that with Vds=3.3V mosfet drain current is at 55A, much higher than fuse allows to.

ghent360, 2021-01-25:
The small eeprom is there so one can make a completely plug & play system. The eeprom would have the driver type and rsense values stored in it.

It is not needed for any current firmware.

ArkadiuszRaj, 2021-01-29:
I have completed routing of the new controller board, and together with this driver carrier board I have placed order at jlpcb.
For 2 preassembled boards, there is no change in price when selecting STM32F427 of 429 variant.

Here are the changes to the original V2 project:
- STM32F429 (obviously)
- Removal of 3x EXP ports
- Reduction from 6 to 2 thermocouple ports using 2x3 pin header/socket, each with dedicated CS signal (no impact on ADC lines)
- Reduction from 5 to 2 ports with static 12/24V
- Reduction from 5 to 2 ports with static 5V
- Changed WIFI header to 2x6 pins
- Changed TF card connecttion to SDIO 4-bit port
- ST_ALARM remapped to ST_ALARM_X, ST_ALARM_Y and ST_ALARM_Z
- Serial connector changed to TFT connector with RESET line

PCB 4 layer: (top - tht) GND, 3V3, 5V, GND (bottom - smd)
Components side:
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

Carrier board:
- voltage polarity protection
- 3 LEDs to show Vin, and from 2x25 header: 5V & 3V
- 8 PCIx slots
- each slot has populated full serial connectinon (TX & RX lanes, compatible to your design)
- each slot has jumper block to map alarm signal to X, Y, Z or common Alarm lines.

PCB 4 layer: Vin, 3V3, 5V, GND
Components side:
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

ArkadiuszRaj, 2021-01-29:
Ouch, newest KiCad 5.99 (kicad-r20550 and later) has issue with zone fillining yet adds something to schema.
Now I can edit in my new Schema but can not import that to old (working) PCBnew :/

ghent360, 2021-01-29:
Congrats, let me know how it turns out.

ArkadiuszRaj, 2021-01-29:
Thanx. Will do.

Waiting for the prototypes I have started to define a new variant in
STM32_duino for STM32F429.
Also I am preparing a new environment to compile RRF using this specific
variant.

BTW, RRF uses TIM1/5 for internal purposes (i.e. TIM1 for SoftUART and TIM5
for stepping).
In V2 you are using PA8 for PWM which is mapped to TIM1_CH1. Thus there is
a clash with current STM32F4 RRF code.

pt., 29 sty 2021 o 22:22 ghent360 <notifications@github.com> napisał(a):

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

ArkadiuszRaj, 2021-01-31:
I have sucessfuly created new board variant and compiled RRF for stm32f429 mcpu with esp8266.

However Andy's framework is tailored to STM32F4 witch he used for further corrections. Thus is it incompatible with other arhcitectures like F7 or H7.

Thinking about FD-CAN, I saw JLCPCB has on their stock STM32H743IIT6 chip which costs €7.1539 (+extended part fee).
This particular chip would be in par with Duet3 one regarding functionality yet 25% faster.

Thus to go with it, a major reconstruction of RRF build framework must be done. I mean to take original Arduino_Core_STM32 and use it to compile F4, H7 variants.

BTW
In the original Core lib I see support for your PrntrBoardV1 & 2 (PRNTR_Vx - single pin definitions!).
In Andy' version there is only V1 (PRNTR_F407_V1)

In my modified build scripts, STM selection is done on the board name, then proper selection of cpu family and procesor code is done. Thus I am able to compile RRF for PrntrBoardV2 if I will  only have proper variant defined.  Wanna play?

ghent360, 2021-01-31:
Andy is using an old version of the stm32duino core as base for the
CoreSTM32F4 repository. That is why there is only v1 or my board.

I have a clone of RRFBuild, CoreSTM32F4 and RepRapFirmware with mods to
compile RRF for the prntrboard v2 and updated to the latest stm32duino
version.

That said the RRF port is not quite complete and it does not work on my
board yet. One issues is that Andy has not ported the part of the code that
can share a serial port to talk to the 2209 steppers. Also there is
something odd with the usb and it does not seem to work yet. I suspect the
SKR has bootloader that is initializing the usb and i don’t have that code.

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

ArkadiuszRaj, 2021-01-31:
Talking aboit USB,.. from where have you taken your bootloader?
I am creating mine by using STM32CubeMX, with all peripherials defined, so i have initialziation of all of them in main()

```
  /* Initialize all configured peripherals */
  MX_GPIO_Init();
  MX_ADC3_Init();
  MX_CAN1_Init();
  MX_I2C1_Init();
  MX_SDIO_SD_Init();
  MX_SPI1_Init();
  MX_SPI2_Init();
  MX_TIM3_Init();
  MX_TIM4_Init();
  MX_USART1_UART_Init();
  MX_USART2_UART_Init();
  MX_USART3_UART_Init();
  MX_USB_OTG_FS_PCD_Init();
  MX_TIM9_Init();
  MX_FATFS_Init();
  /* USER CODE BEGIN 2 */
```
I know almost everything is not used, still  teh final binary code is less than 32kB, so it fits in first two FLASH meory banks.
So the only question is what parts of the perifperal clocks are deconfigured before jumping to the firmware part.

ghent360, 2021-01-31:
I also used the CubeMX to generate the startup code, but I wanted to fit in
16k, so only use minimal peripherals SDIO and some LEDs. I tried to
de-configure all clocks before jumping to the main app to try and mimic the
reset state. I don't think there is a strict rule, as long the main app is
not confused by the bootloader settings it should be ok.

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

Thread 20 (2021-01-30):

FD-CAN or not...

ArkadiuszRaj, 2021-01-30:
First of all thx!!!! After dowloading  gcc-arm-none-eabi-10-2020-q4-major-aarch64 onto my little ARM machine, compilation of RRF works smoothly.

Now The Part To Discusss.

Duet3 uses not CAN. Hardware-wise is prepared for another standard: FD-CAN.
With current PrntrBoardV2 update there is simple CAN interface, not the flexible data-rate alternatve.
I mean both STM32 and the TJA chip supports CAN upt o 1 or 2 Mbps.

Personally I do not believe that FD-CAN is really needed to adress hotend board and sychronize extruder steps with other kinematics. But I have started to think. For whole planned Duet CAN' ecosystem maybe t is worth to use FD CAN.

What can I do? While awaiting for prototype of my variant, will most probably buy Duet 3 Toolboard 1LC and give it a try. I mean will try to connect is that to CAN.

If this will work, that will be superb.
If not - then I guess swicth to STM32H7 would be necessary.

With this issue I wanted to make you aware of my doubts on this topic.

ghent360, 2021-01-31:
That seems like a problem. The all Duet3 boards seem to be CAN-FD and I can
see in the code #if USE_NEW_CAN_DRIVER <can fd stuff>.
The main issue is that can-fd supports 64-byte data messages, where can is
only up to 8 and the RRF code does use messages longer than 8 bytes. I
don't know if these are broken into smaller chunks and re-constructed  in
the "Old driver" code. But even if that is so, you will have to re-compile
the expansion firmware with different settings and hope it still works.

~V

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

ArkadiuszRaj, 2021-01-31:
CAN frames are not interchangable, what I ment was using FD-CAN in CAN 2.0 compatibility mode. New message format in CAN 2 network will be seen as error.

Well, the first and the most important step is to port CAN communication to STM32 which as I understand is not yet done.

As for Today, RRF support clasical CAN and FD-CAN that comes either from CoreN2G (we do not use) or as driver from hardware "abstraction" for SAME7 mcpu. My idea was to go into drirection to create other driver.

ghent360, 2021-01-31:
Yes you can create a driver based on the CAN 2.0 hw in the STM, but I don't
think it would be able to talk to Duet3
Toolboard and the likes.

Migrating RRF to STM32F7 should be doable, there is not that much F4
specific code even though the repo is called CoreSTM32F4. Most of the code
works through the Arduino core library, which has been ported to F7. The
Arduino core just works over the HAL or LL code layers from ST micro.

Supporting H7 is a different story, the chip internal structure is much
more complicated than the F7 with multiple busses and power domains. I
would probably just wait for Frederic from ST to complete the arduino port.

btw. you can contact me at ghent360 at iquiry.us

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

ArkadiuszRaj, 2021-01-31:
Andys CoreSTM32F4 is not compiling for F7 variant. Already check that.
But you are right, that is why I am focusing on building bulid scripts to utilize Arduino_Core libarry rather the Andy one.

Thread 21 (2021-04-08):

The latest version downloaded by KICAD cannot open the file

chinamore, 2021-04-08:
Stable Release
Current Version: 5.1.9

ghent360, 2021-04-08:
Correct. You would need the new Kicad 6 nightly builds.

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

Closed 2021-05-02.

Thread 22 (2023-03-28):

Blog seems down.

programpro2005, 2023-03-28:
So it looks like you're blog https://blog.pcbxprt.com/index.php/category/prntrboard/ is inaccessible to me. I wanted to see your updates as i wanted to build one myself but pinging you're blog doesn't respond down detector says it's down and chrome and Firefox can't reach it. If you don't use the blog anymore then removing the links would be a good idea.

ghent360, 2023-03-29:
Try
https://web.archive.org/web/20211124225828/https://blog.pcbxprt.com/index.php/category/prntrboard/

On Tue, Mar 28, 2023 at 6:28 AM programpro2005 ***@***.***>
wrote:

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

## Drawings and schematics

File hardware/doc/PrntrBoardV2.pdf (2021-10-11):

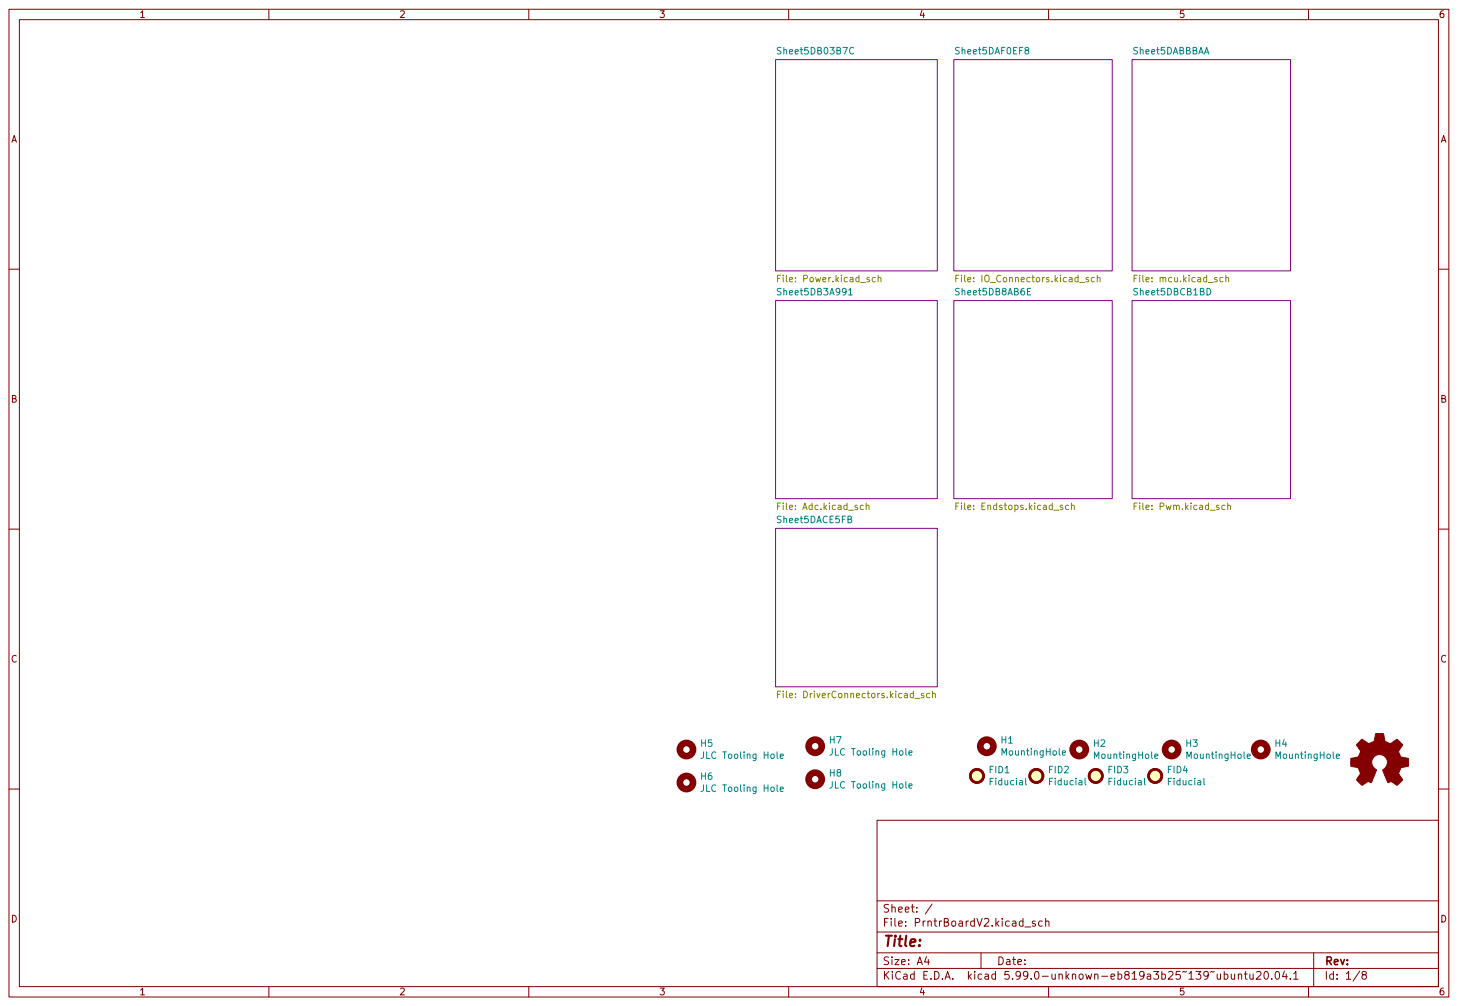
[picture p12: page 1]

File: Endstops.kicad_sch Sheet5DB3A991 File: Adc.kicad_sch

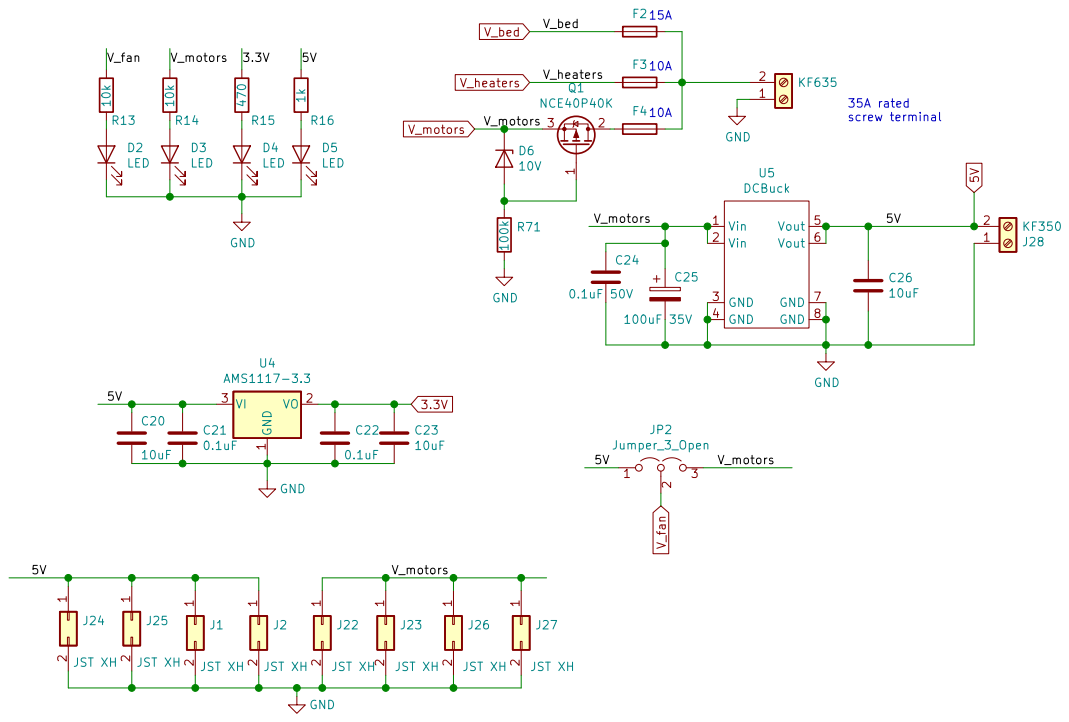
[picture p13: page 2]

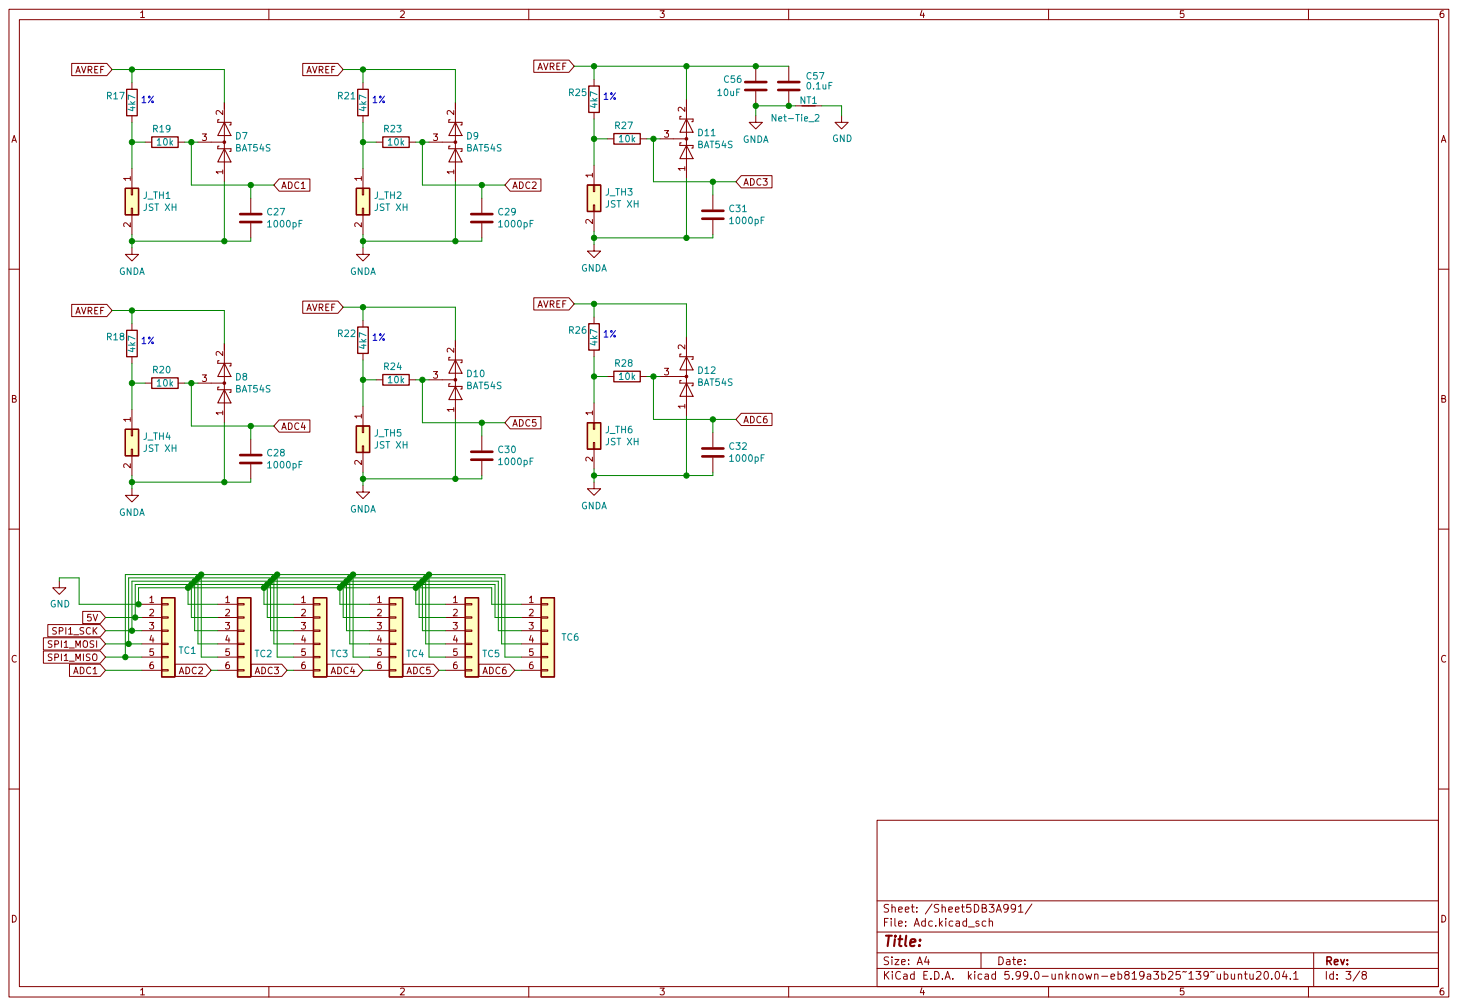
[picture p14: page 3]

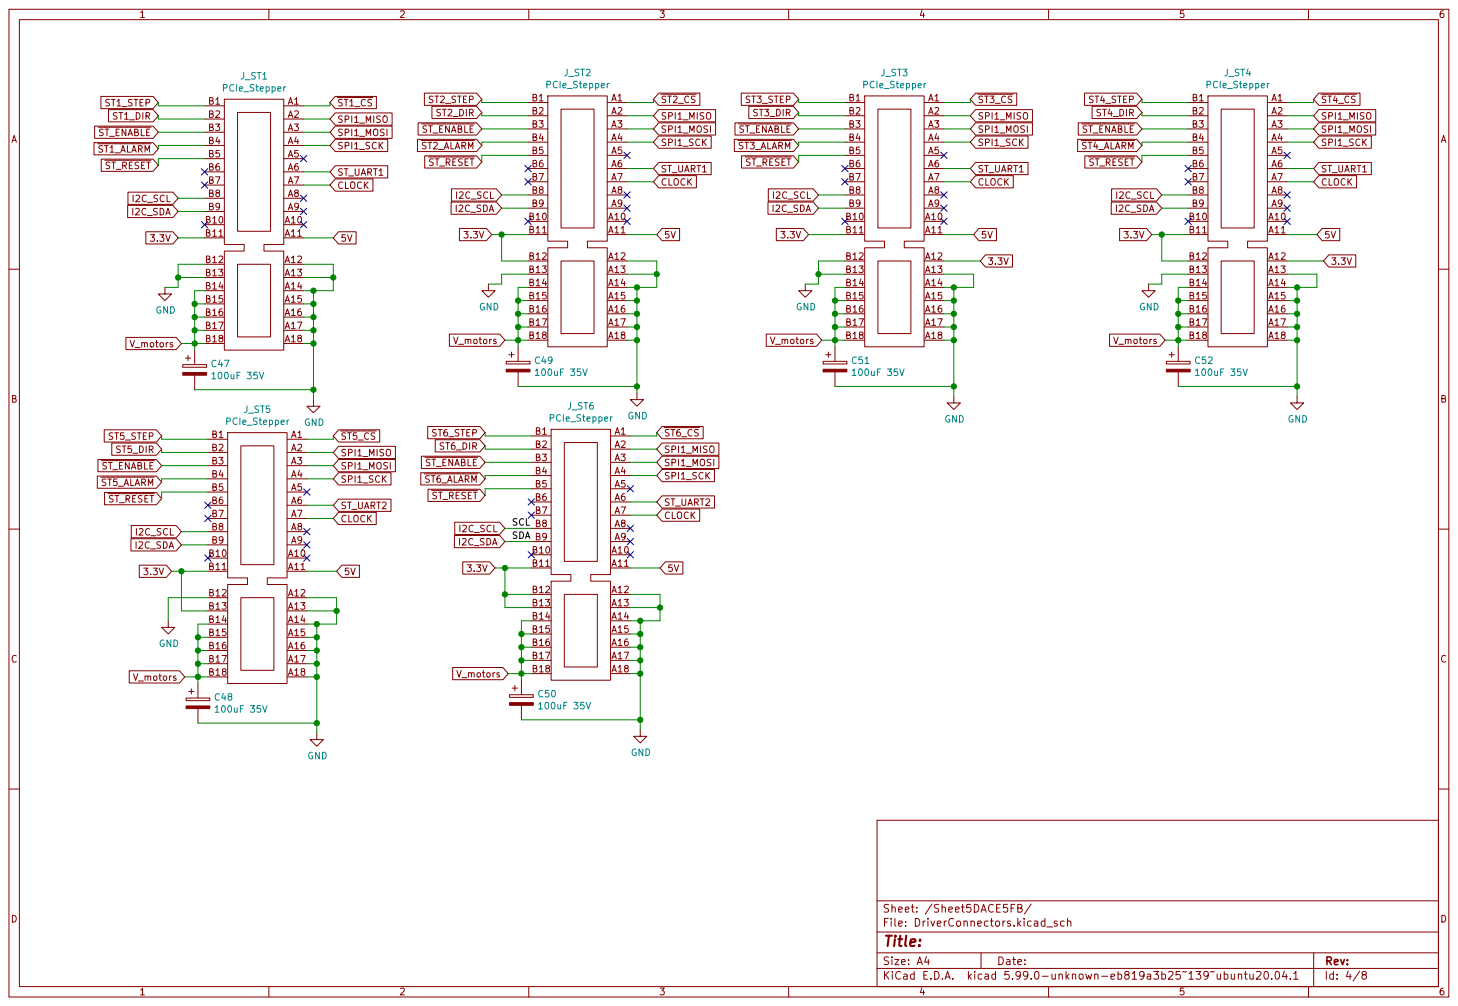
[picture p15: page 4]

File: DriverConnectors.kicad_sch Sheet: /Sheet5DACE5FB/ GND

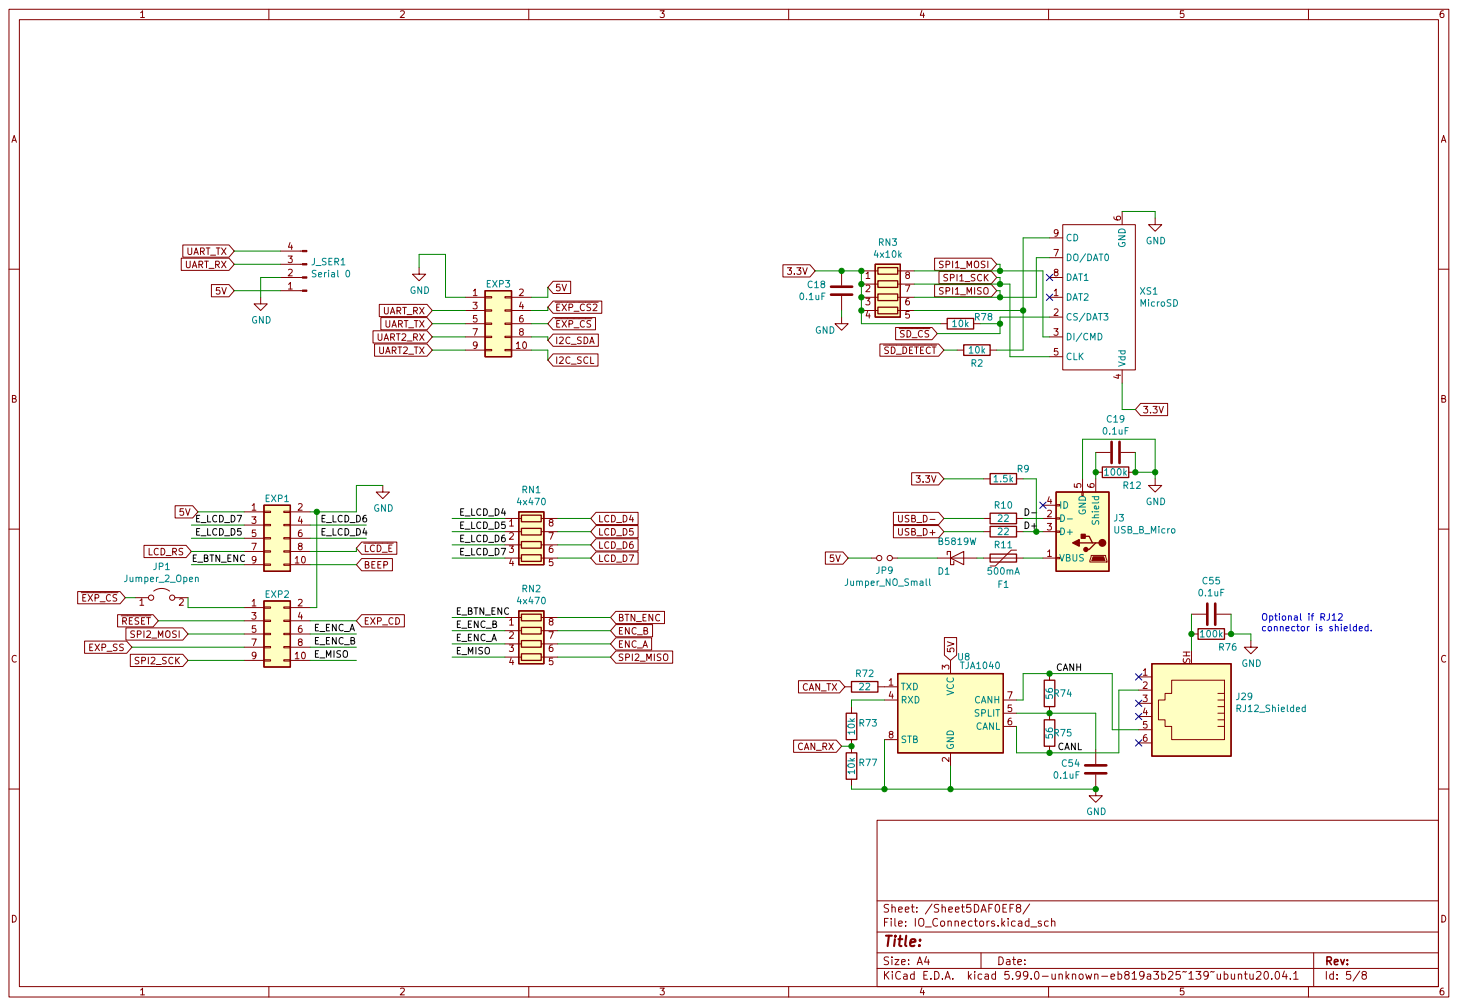
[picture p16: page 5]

6 DO/DAT0 7 DAT1 8 CD 9 XS1 MicroSD GND
SPI1_SCK USB_D+ SPI1_MISO

Optional if RJ12 connector is shielded.

3 RXD 4 SPLIT 5 CANL 6 CANH 7 STB 8 U8TJA1040 R72

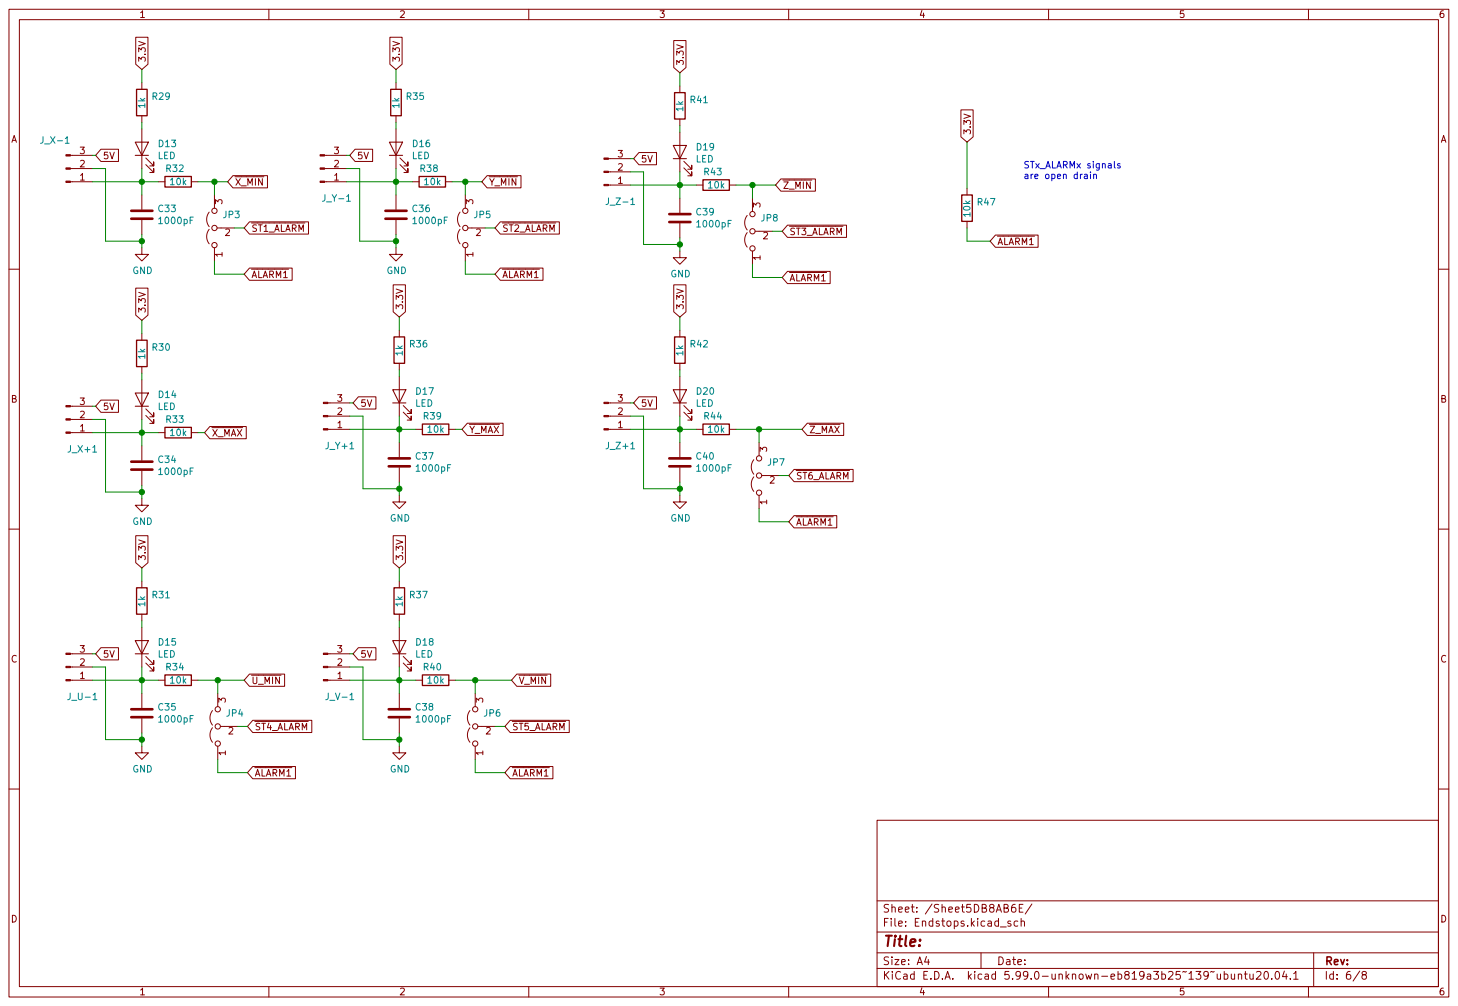
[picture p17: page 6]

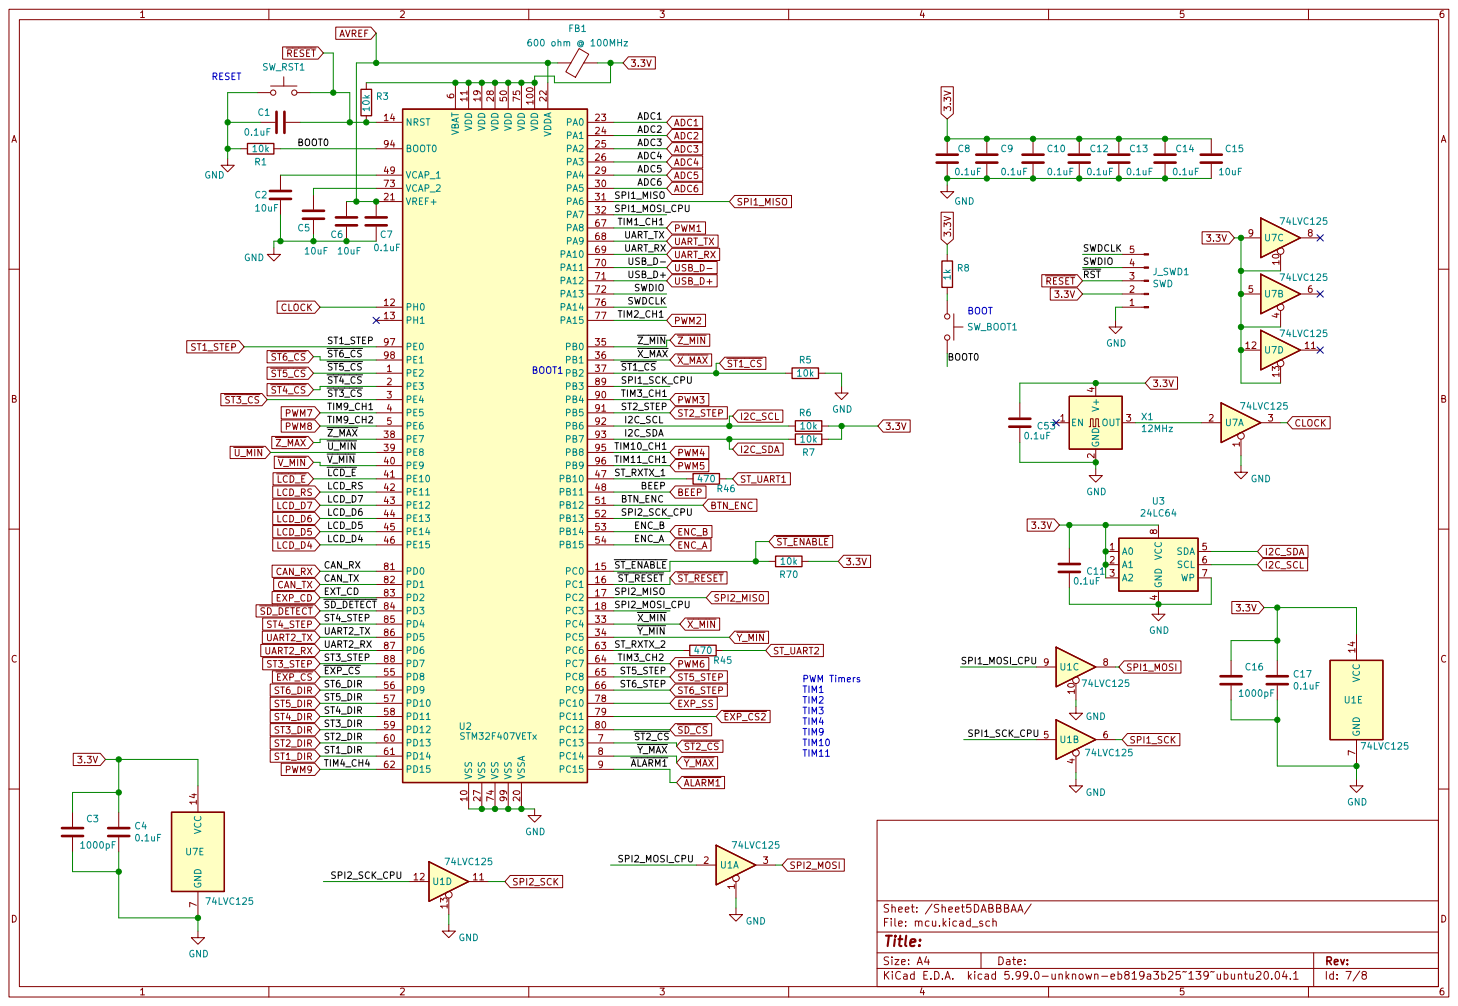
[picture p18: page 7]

4 SDA 5 SCL 6 WP 7 VCC

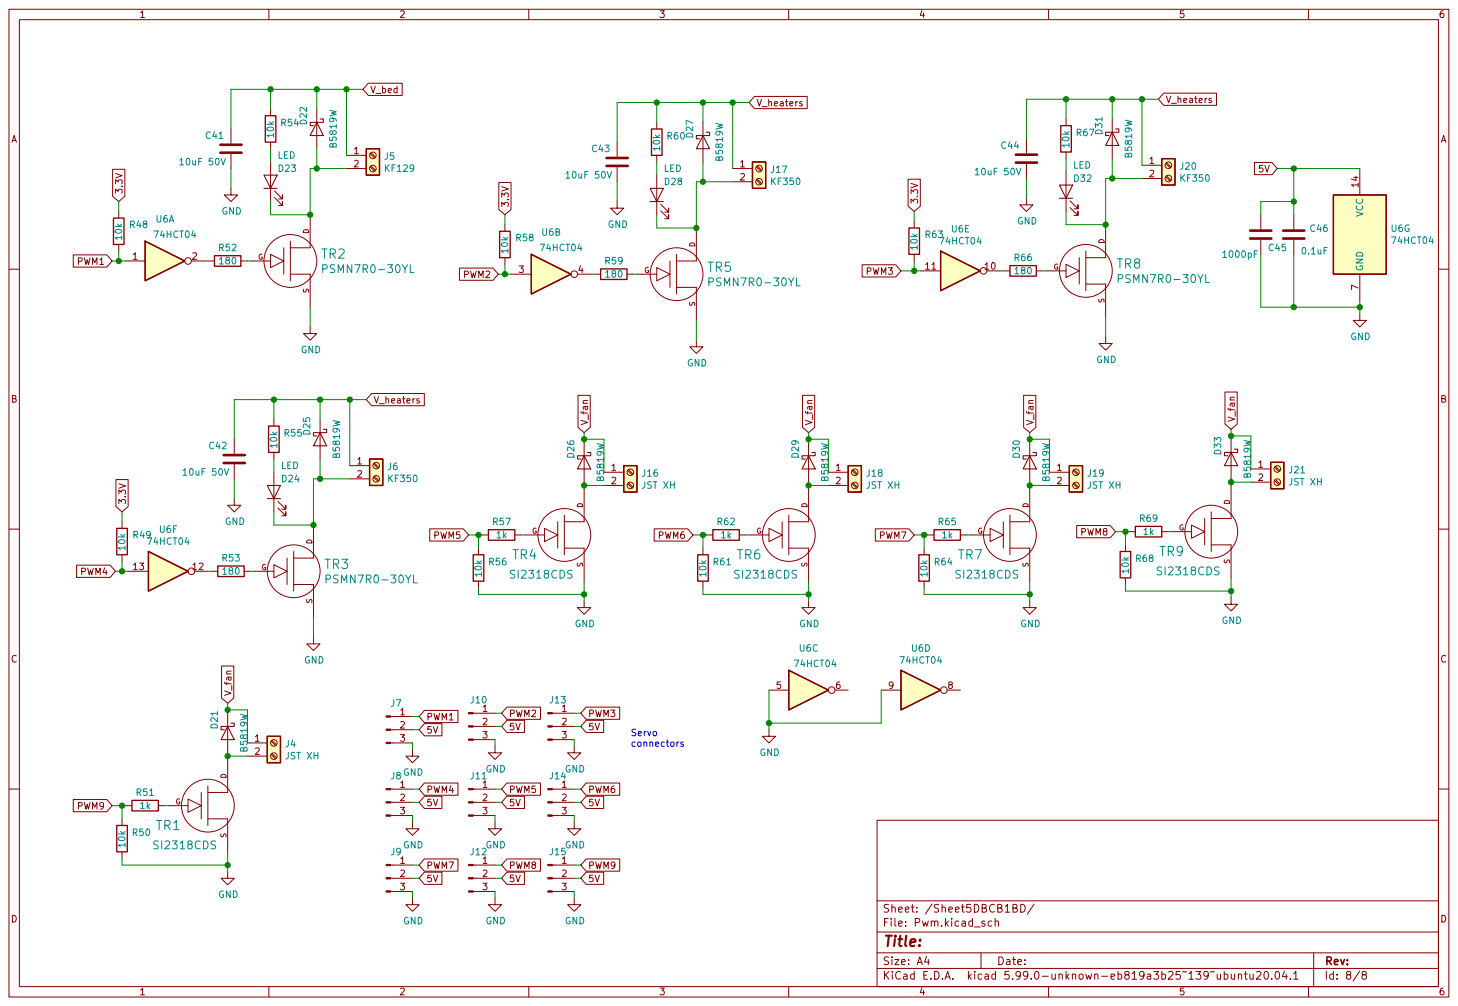
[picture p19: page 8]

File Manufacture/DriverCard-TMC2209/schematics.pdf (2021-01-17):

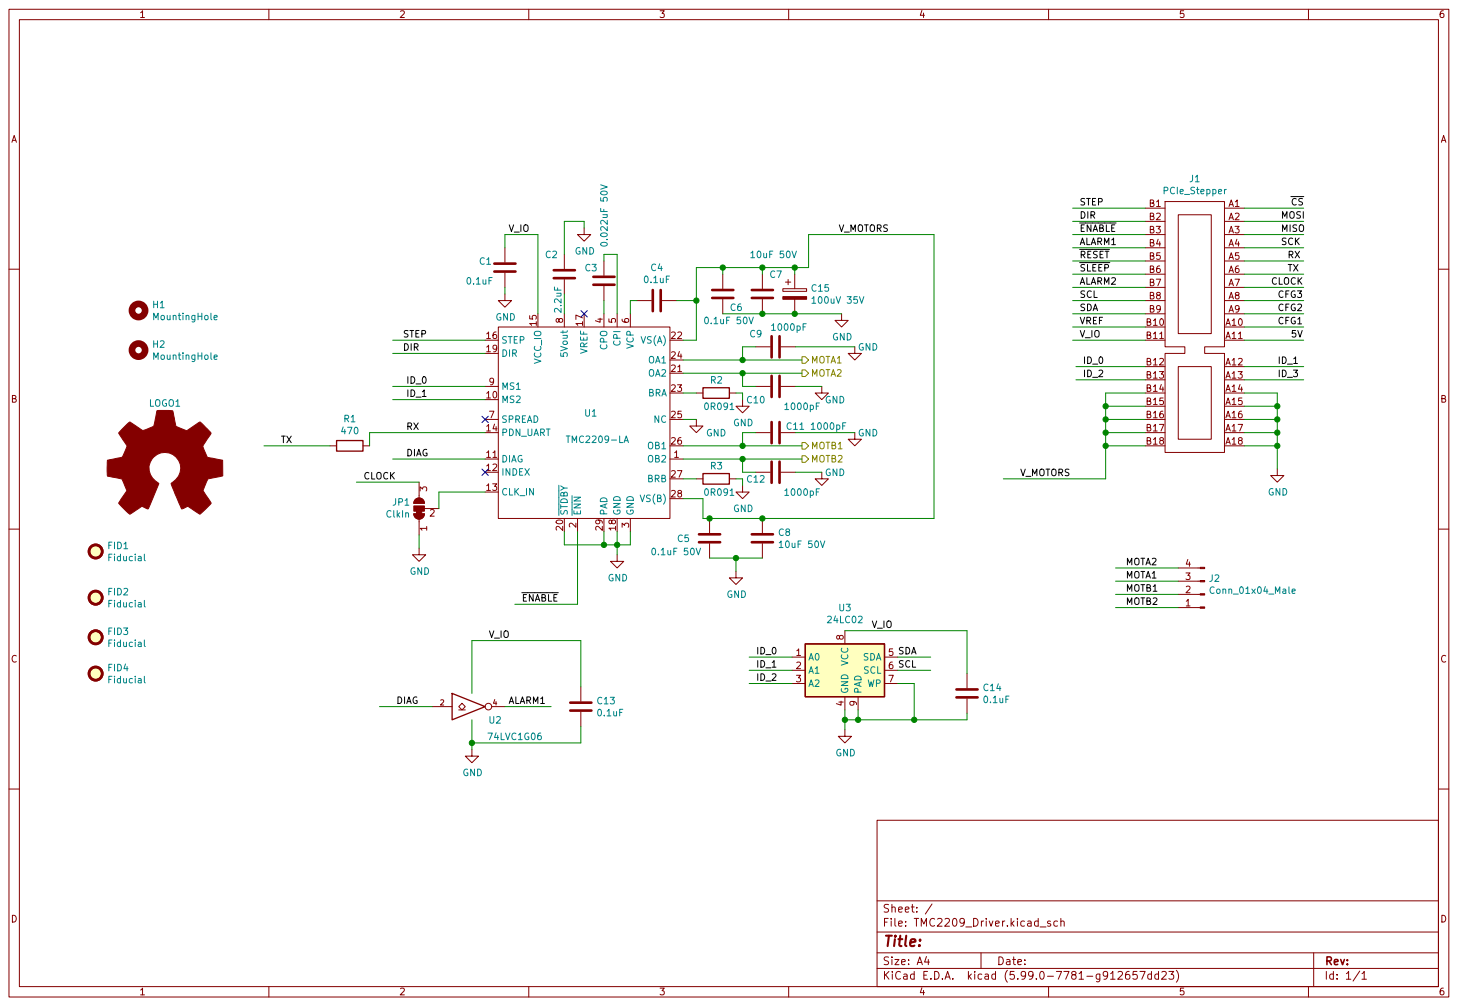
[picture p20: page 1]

2 ~STDBY 20 OA2 21 VS(A) 22 BRA 23 OA1 24 NC 25 OB1 26 BRB 27 VS(B) 28 PAD 29 GND

File: TMC2209_Driver.kicad_sch Sheet: / GND GND

4 SDA 5 SCL 6 WP 7 VCC

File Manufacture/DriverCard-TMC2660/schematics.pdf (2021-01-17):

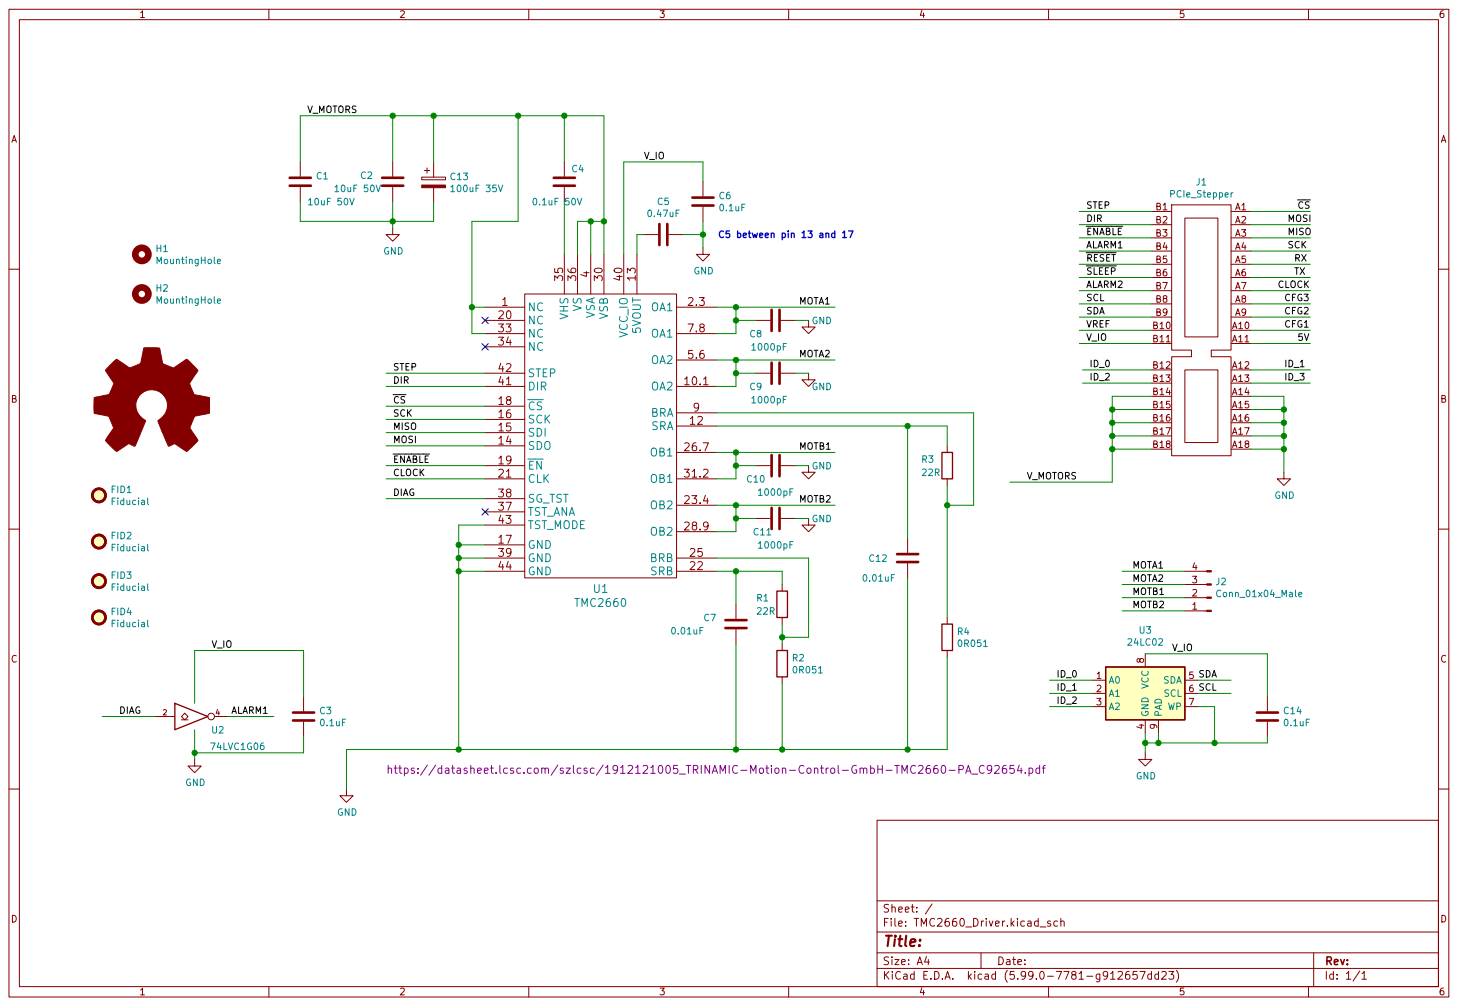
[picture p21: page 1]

4 VCC_IO 40 DIR 41 STEP 42 TST_MODE 43 GND 44 OA2 5.6 OA1 7.8 BRA 9 U1 TMC2660

4 SDA 5 SCL 6 WP 7 VCC

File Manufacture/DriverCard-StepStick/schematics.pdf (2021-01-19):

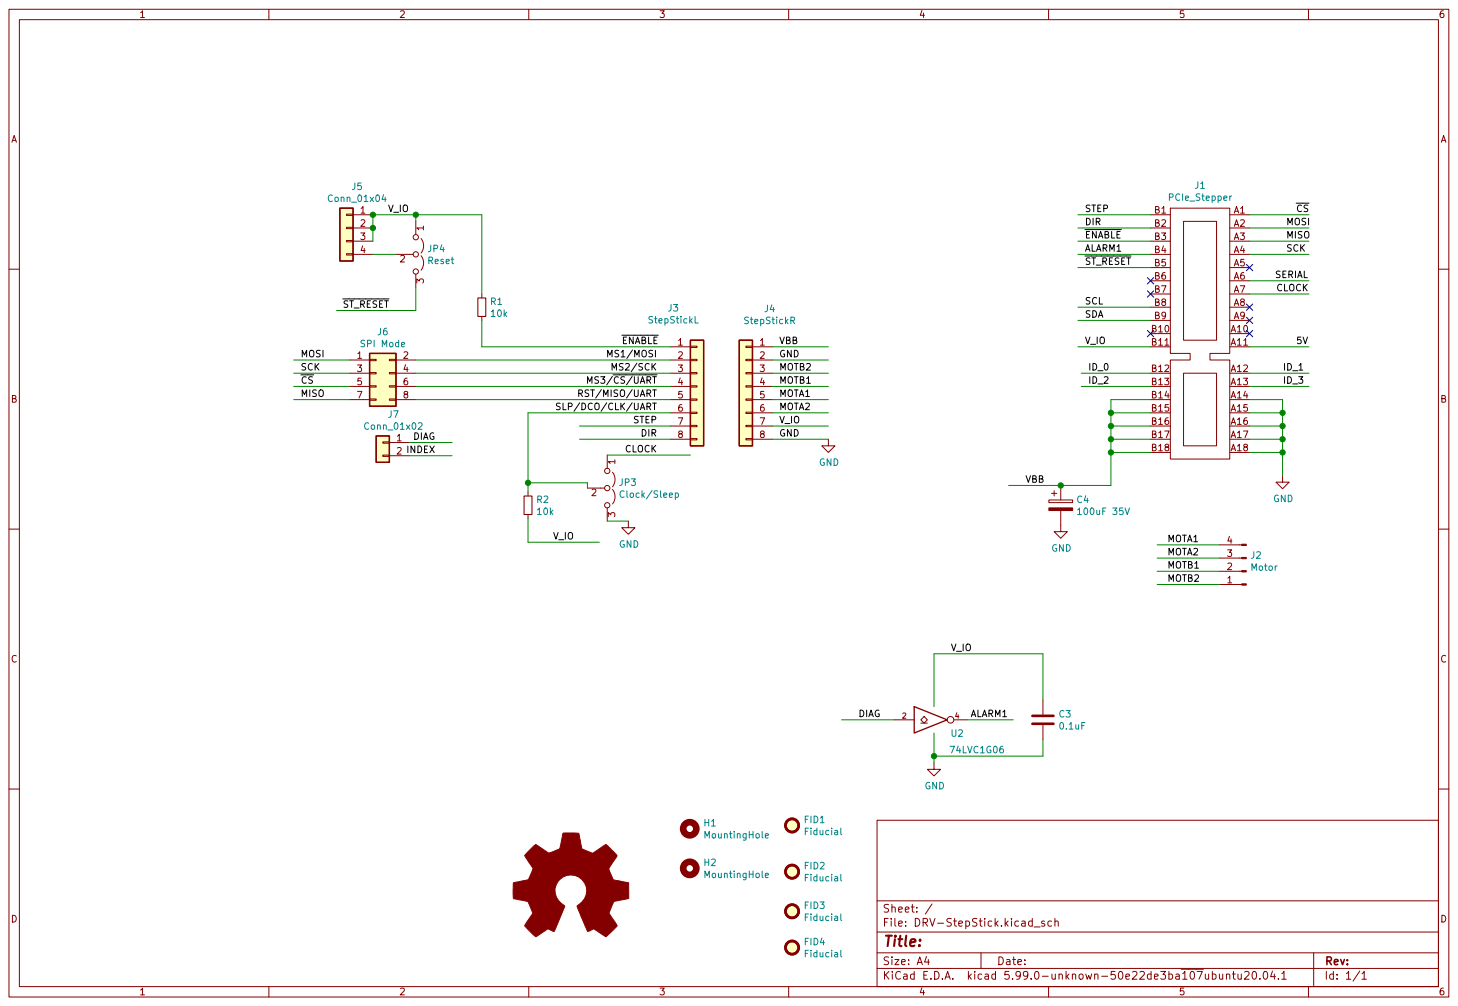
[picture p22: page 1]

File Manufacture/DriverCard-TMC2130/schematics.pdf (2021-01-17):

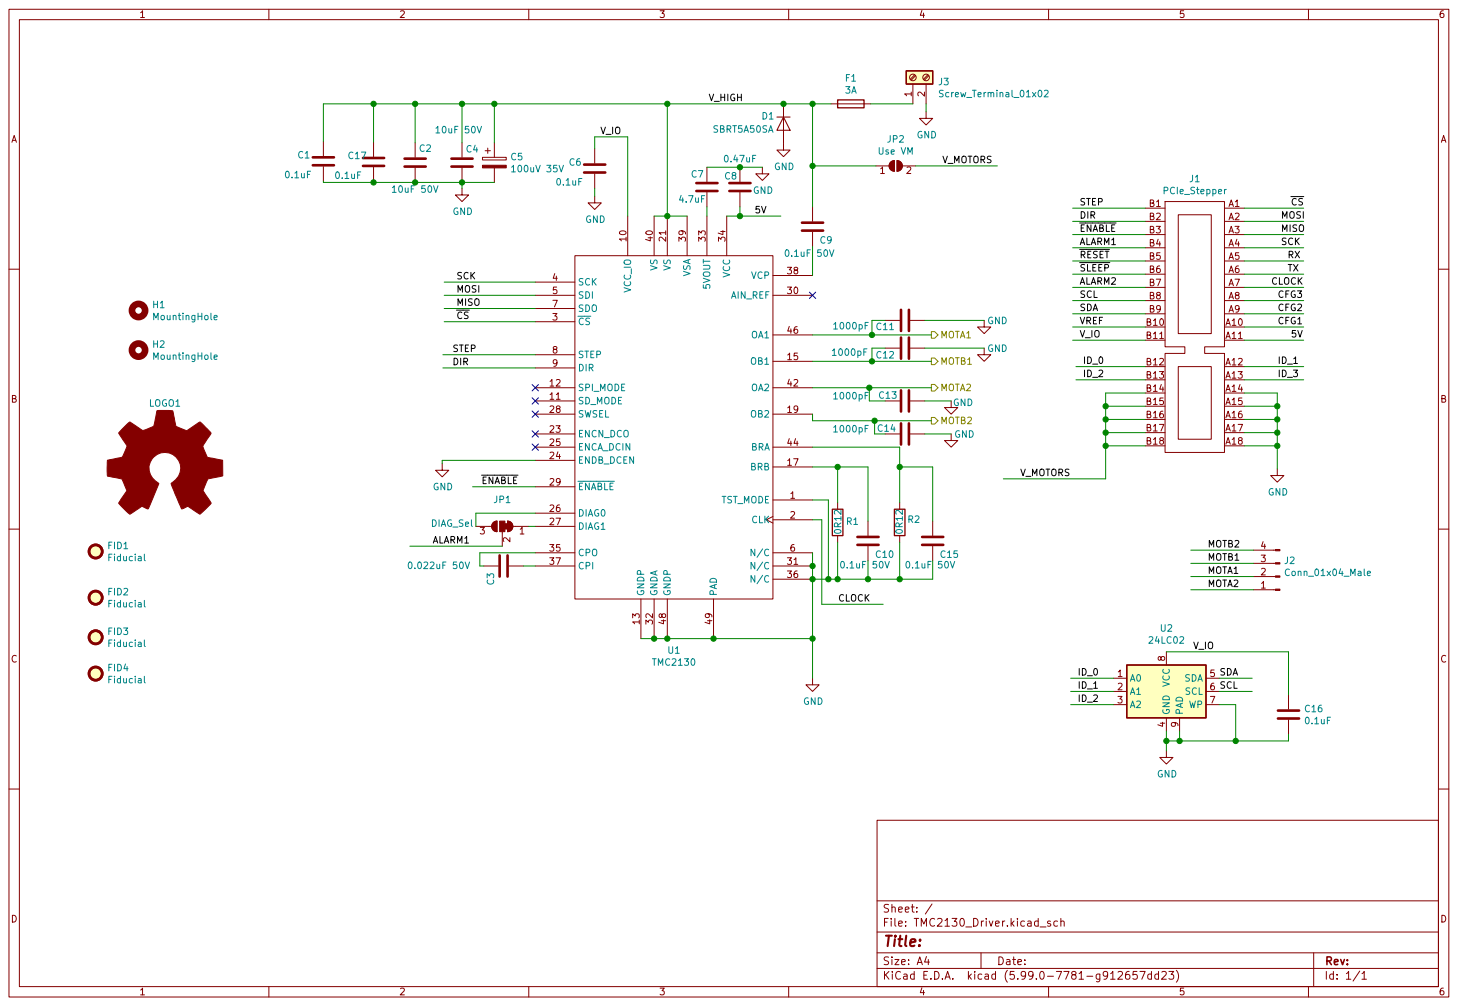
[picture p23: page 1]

4 SDA 5 SCL 6 WP 7 VCC


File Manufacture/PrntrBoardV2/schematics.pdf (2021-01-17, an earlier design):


File: Endstops.kicad_sch Sheet5DB3A991 File: Adc.kicad_sch




File: DriverConnectors.kicad_sch Sheet: /Sheet5DACE5FB/ GND


6 DO/DAT0 7 DAT1 8 CD 9 XS1 MicroSD GND 56R75 TXD 1 GND
~SD_DETECT 5V

2 | | 7 SD_MISO

3 RXD 4 SPLIT 5 CANL 6 CANH 7 STB 8 U8TJA1040 R73 10k 56R74 R72



6 VCAP_1 49 VCAP_2 73 VDD 100 VDD 11 VDD 19 VDD 28 VDD 50 VDD 75 VDDA 22 VREF+ 21 VSS 10 VSS 27 VSS 74 VSS 99 VSSA 20 U2STM32F407VETx C53
74LVC125 R3 10k

J_SWD1 SWD GNDGND VCC 14 GND

4 SDA 5 SCL 6 WP 7 VCC


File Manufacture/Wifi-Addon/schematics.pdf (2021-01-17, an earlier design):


1 VO 2 VI 3 U1 AMS1117-3.3 D1B5819W GND GND GND

3 ~RTS 4 ~CTS 5 TNOW 6 VCC
TX USB_D- USB_D+ RX

File: WiFi-Addon.kicad_sch Sheet: /
Id: 1/1 Title:

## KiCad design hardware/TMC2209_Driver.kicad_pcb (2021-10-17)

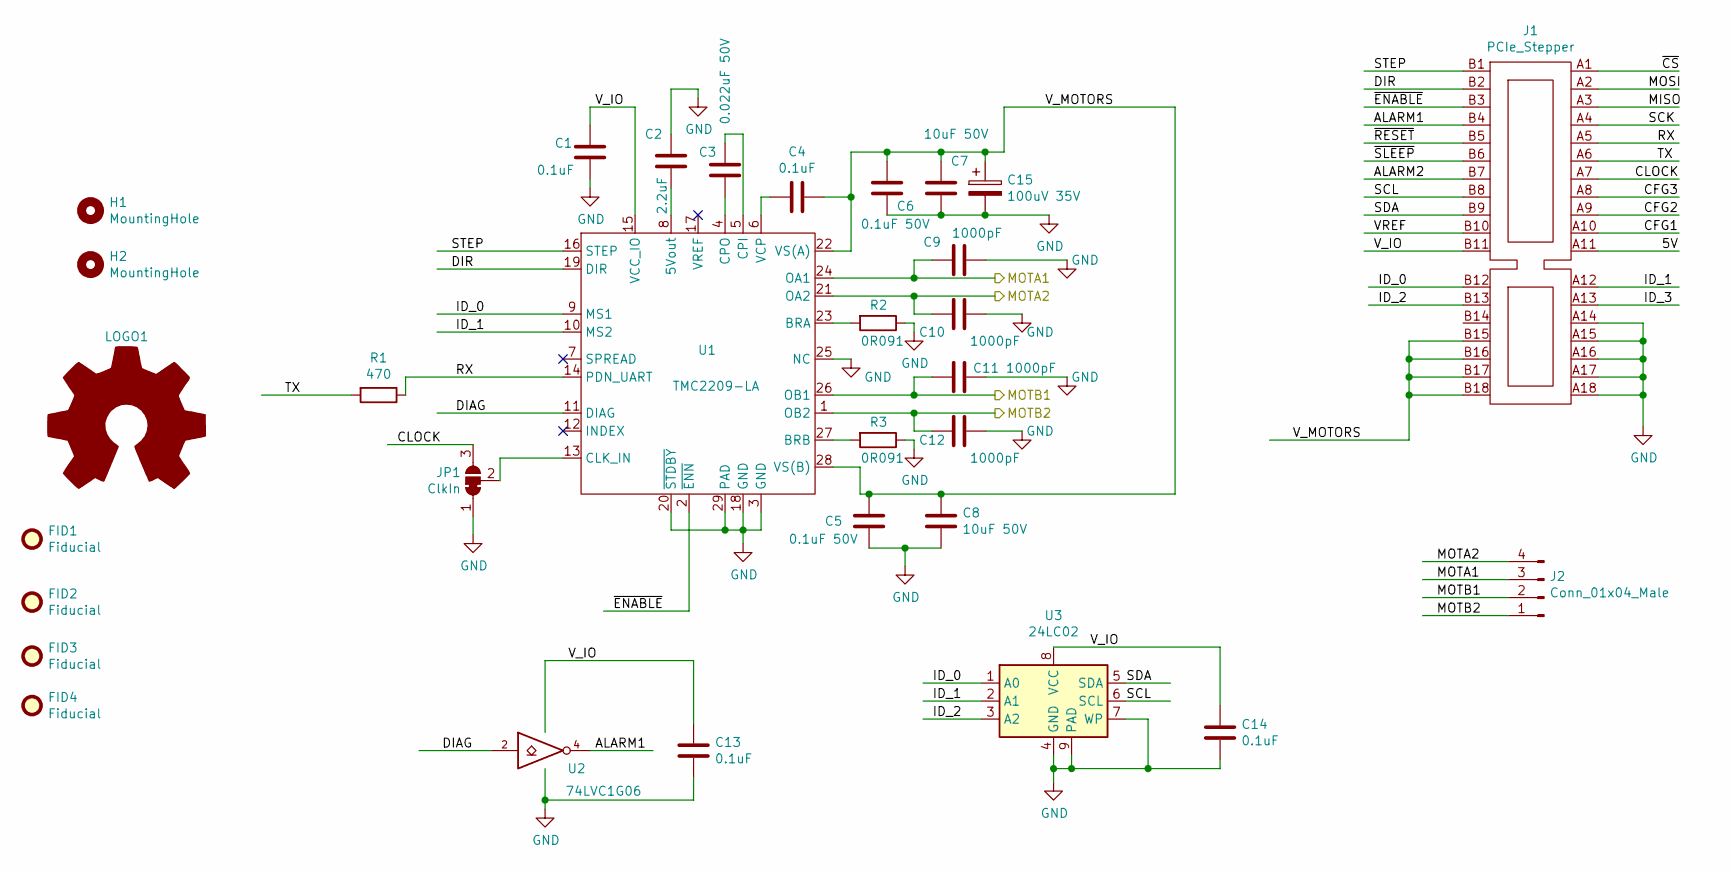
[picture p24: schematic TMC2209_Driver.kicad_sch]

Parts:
C1, C4, C13, C14: 0.1uF; C_0603_1608Metric; Part # CC0603KRX7R9BB104; LCSC Part # C14663
C2: 2.2uF; C_0603_1608Metric; Part # CL10A225KO8NNNC; LCSC Part # C23630
C3: 0.022uF 50V; C_0603_1608Metric; Part # CL10B223KB8NNNC; LCSC Part # C21122
C5, C6: 0.1uF 50V; C_0402_1005Metric; Part # CL05B104KO5NNNC; LCSC Part # C1525
C7, C8: 10uF 50V; C_1206_3216Metric; Part # CL31A106KBHNNNE; LCSC Part # C13585
C9, C10, C11, C12: 1000pF; C_0603_1608Metric; Part # CL10B102KB8NNNC; LCSC Part # C1588
C15: 100uV 35V; CP_Elec_6.3x7.7; Part # VE-101M1VTR-0607; LCSC Part # C171732
FID1, FID2, FID3, FID4: Fiducial; Fiducial_1mm_Dia_2.54mm_Outer_CopperTop
H1, H2: MountingHole; MountingHole_2.7mm_M2.5
J1: PCIe_Stepper; BUS_PCIexpress
J2: Conn_01x04_Male; Molex-SL-4POS
JP1: ClkIn; SolderJumper-3_P1.3mm_Bridged12_Pad1.0x1.5mm
LOGO1: Logo_Open_Hardware_Large; OSHW-Logo2_7.3x6mm_SilkScreen
R1: 470; R_0603_1608Metric; Part # 0603WAF4700T5E; LCSC Part # C23179
R2, R3: 0R091; R_1210_3225Metric; Part # 1206W3F910MT5E; LCSC Part # C247542
U1: TMC2209-LA; TMC22xx_QFN; Part # TMC2209-LA; LCSC Part # C465949
U2: 74LVC1G06; SOT-353_SC-70-5; Part # 74LVC1G06GW,125; LCSC Part # C426704
U3: 24LC02; TDFN-8-1EP_3x2mm_P0.5mm_EP1.56x1.45mm; Part # CAT24C02VP2IGT3A; LCSC Part # C184154

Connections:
/5V: J1.A11
/ALARM1: J1.B4, U2.4
/ALARM2: J1.B7
/CFG1: J1.A10
/CFG2: J1.A9
/CFG3: J1.A8
/CLOCK: J1.A7, JP1.3 (B)
/DIAG: U1.11 (DIAG), U2.2
/DIR: J1.B2, U1.19 (DIR)
/ID_0: J1.B12, U1.9 (MS1), U3.1 (A0)
/ID_1: J1.A12, U1.10 (MS2), U3.2 (A1)
/ID_2: J1.B13, U3.3 (A2)
/ID_3: J1.A13
/MISO: J1.A3
/MOSI: J1.A2
/MOTA1: C9.2, J2.3, U1.24 (OA1)
/MOTA2: C10.2, J2.4, U1.21 (OA2)
/MOTB1: C11.2, J2.2, U1.26 (OB1)
/MOTB2: C12.2, J2.1, U1.1 (OB2)
/RX: J1.A5, R1.1, U1.14 (PDN_UART)
/SCK: J1.A4
/SCL: J1.B8, U3.6 (SCL)
/SDA: J1.B9, U3.5 (SDA)
/STEP: J1.B1, U1.16 (STEP)
/TX: J1.A6, R1.2
/VREF: J1.B10
/V_MOTORS: C4.1, C5.1, C6.1, C7.1, C8.1, C15.1, J1.B15, J1.B16, J1.B17, J1.B18, U1.22 (VS(A)), U1.28 (VS(B))
/~CS: J1.A1
/~ENABLE: J1.B3, U1.2 (~ENN)
/~RESET: J1.B5
/~SLEEP: J1.B6
GND: C1.2, C2.1, C5.2, C6.2, C7.2, C8.2, C9.1, C10.1, C11.1, C12.1, C13.2, C14.2, C15.2, J1.A14, J1.A15, J1.A16, J1.A17, J1.A18, JP1.1 (A), R2.1, R3.1, U1.3 (GND), U1.18 (GND), U1.20 (~STDBY), U1.25 (NC), U1.29 (PAD), U2.3 (GND), U3.4 (GND), U3.7 (WP), U3.9 (PAD)
unnamed: C2.2, U1.8 (5Vout)
unnamed: C3.1, U1.5 (CPI)
unnamed: C3.2, U1.4 (CPO)
unnamed: C4.2, U1.6 (VCP)
unnamed: JP1.2 (C), U1.13 (CLK_IN)
unnamed: R2.2, U1.23 (BRA)
unnamed: R3.2, U1.27 (BRB)
VCC: C1.1, C13.1, C14.1, J1.B11, U1.15 (VCC_IO), U2.5 (VCC), U3.8 (VCC)

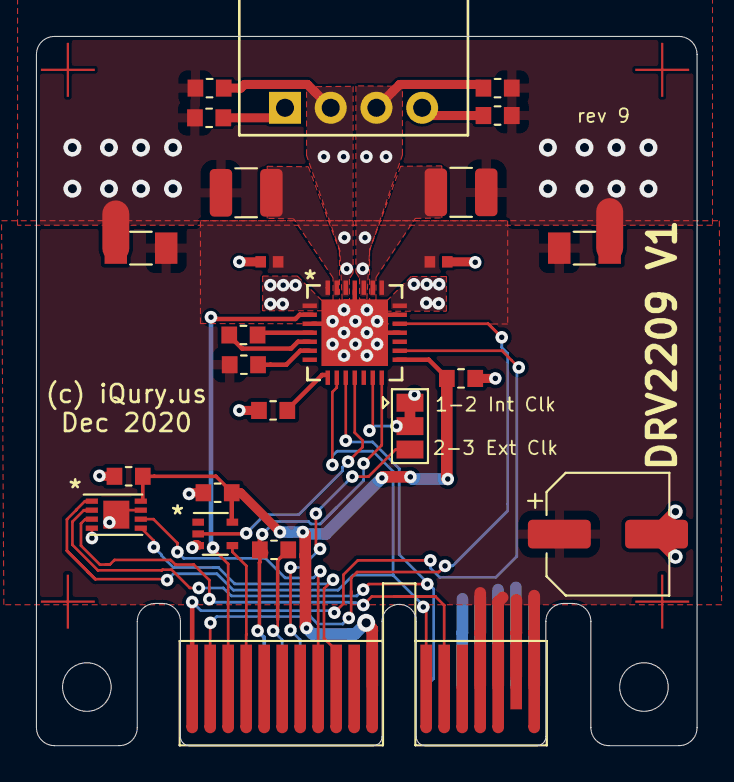
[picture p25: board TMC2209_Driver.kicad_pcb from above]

Board: 2 copper layers, 36.7 x 39.4 mm, 31 parts (1 on the bottom side), 27 nets.

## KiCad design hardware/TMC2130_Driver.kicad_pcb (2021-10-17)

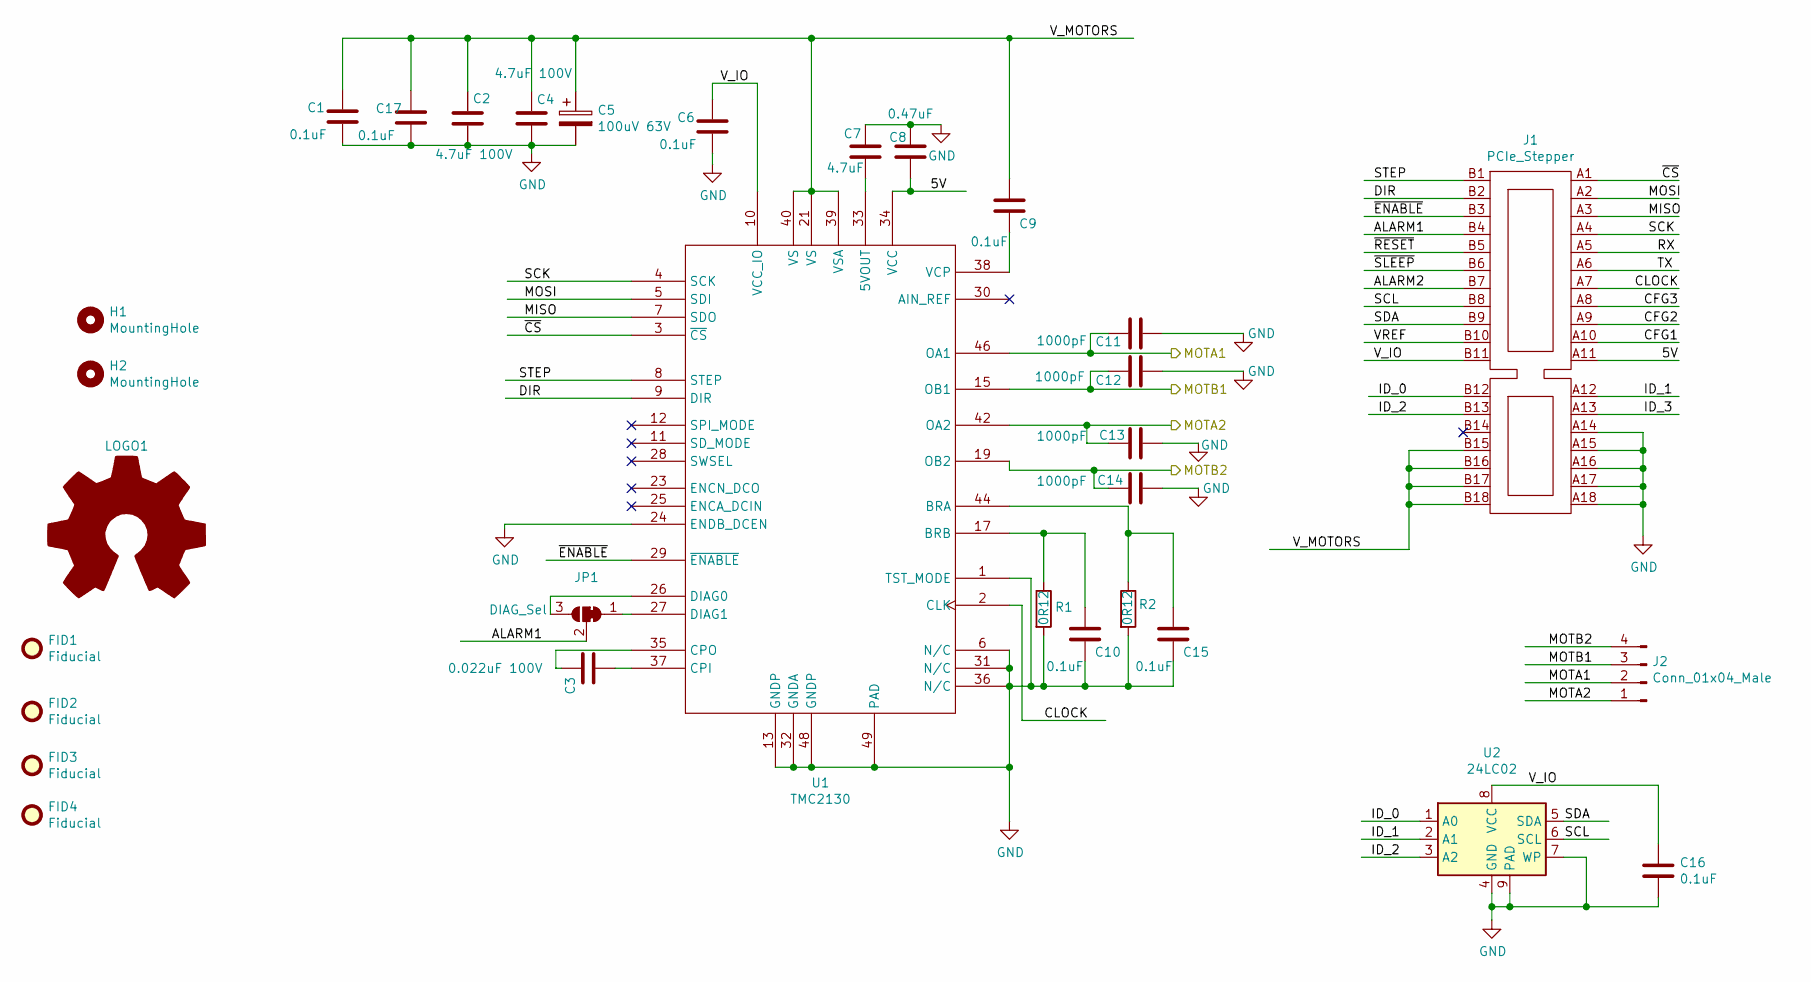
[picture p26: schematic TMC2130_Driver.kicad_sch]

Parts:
C1, C9, C17: 0.1uF; C_0805_2012Metric; Part # CL21B104KCFNNNE; LCSC Part # C28233
C2, C4: 4.7uF 100V; C_1210_3225Metric; Part # HMK325C7475KN-TE; LCSC Part # C697607
C3: 0.022uF 100V; C_0805_2012Metric; Part # CC0603KRX7R0BB223; LCSC Part # C313105
C5: 100uV 63V; CP_Elec_10x10.5; Part # CK1J101MCRG10; LCSC Part # C263945
C6, C16: 0.1uF; C_0603_1608Metric; Part # CC0603KRX7R9BB104; LCSC Part # C14663
C7: 4.7uF; C_0603_1608Metric; Part # CL10A475KO8NNNC; LCSC Part # C19666
C8: 0.47uF; C_0603_1608Metric; Part # CL10B474KA8NNNC; LCSC Part # C1623
C10, C15: 0.1uF; C_0805_2012Metric; Part # HMK325C7475KN-TE; LCSC Part # C28233
C11, C12, C13, C14: 1000pF; C_0603_1608Metric; Part # CL10B102KC8NNNC; LCSC Part # C153291
FID1, FID2, FID3, FID4: Fiducial; Fiducial_1mm_Dia_2.54mm_Outer_CopperTop
H1, H2: MountingHole; MountingHole_2.7mm_M2.5
J1: PCIe_Stepper; BUS_PCIexpress
J2: Conn_01x04_Male; Molex-SL-4POS
JP1: DIAG_Sel; SolderJumper-3_P1.3mm_Bridged12_Pad1.0x1.5mm
LOGO1: Logo_Open_Hardware_Large; OSHW-Logo2_7.3x6mm_SilkScreen
R1, R2: 0R12; R_2512_6332Metric; Part # 25121WF120LT4E; LCSC Part # C81248
U1: TMC2130; tmc5130-nc; Part # TMC2130A-TA; LCSC Part # C328952
U2: 24LC02; TDFN-8-1EP_3x2mm_P0.5mm_EP1.56x1.45mm; Part # CAT24C02VP2IGT3A; LCSC Part # C184154

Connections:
/5V: C8.1, J1.A11, U1.34 (VCC)
/ALARM1: J1.B4, JP1.2 (C)
/ALARM2: J1.B7
/CFG1: J1.A10
/CFG2: J1.A9
/CFG3: J1.A8
/CLOCK: J1.A7, U1.2 (CLK)
/DIR: J1.B2, U1.9 (DIR)
/ID_0: J1.B12, U2.1 (A0)
/ID_1: J1.A12, U2.2 (A1)
/ID_2: J1.B13, U2.3 (A2)
/ID_3: J1.A13
/MISO: J1.A3, U1.7 (SDO)
/MOSI: J1.A2, U1.5 (SDI)
/MOTA1: C11.2, J2.2, U1.46 (OA1)
/MOTA2: C13.2, J2.1, U1.42 (OA2)
/MOTB1: C12.2, J2.3, U1.15 (OB1)
/MOTB2: C14.2, J2.4, U1.19 (OB2)
/RX: J1.A5
/SCK: J1.A4, U1.4 (SCK)
/SCL: J1.B8, U2.6 (SCL)
/SDA: J1.B9, U2.5 (SDA)
/STEP: J1.B1, U1.8 (STEP)
/TX: J1.A6
/VREF: J1.B10
/V_IO: C6.1, C16.1, J1.B11, U1.10 (VCC_IO), U2.8 (VCC)
/V_MOTORS: C1.1, C2.1, C4.1, C5.1, C9.1, C17.1, J1.B15, J1.B16, J1.B17, J1.B18, U1.21 (VS), U1.39 (VSA), U1.40 (VS)
/~CS: J1.A1, U1.3 (~CS)
/~ENABLE: J1.B3, U1.29 (~ENABLE)
/~RESET: J1.B5
/~SLEEP: J1.B6
GND: C1.2, C2.2, C4.2, C5.2, C6.2, C7.1, C8.2, C10.2, C11.1, C12.1, C13.1, C14.1, C15.2, C16.2, C17.2, J1.A14, J1.A15, J1.A16, J1.A17, J1.A18, R1.2, R2.2, U1.1 (TST_MODE), U1.6 (N/C), U1.13 (GNDP), U1.24 (ENDB_DCEN), U1.31 (N/C), U1.32 (GNDA), U1.36 (N/C), U1.48 (GNDP), U1.49 (PAD), U2.4 (GND), U2.7 (WP), U2.9 (PAD)
unnamed: C3.1, U1.35 (CPO)
unnamed: C3.2, U1.37 (CPI)
unnamed: C7.2, U1.33 (5VOUT)
unnamed: C9.2, U1.38 (VCP)
unnamed: C10.1, R1.1, U1.17 (BRB)
unnamed: C15.1, R2.1, U1.44 (BRA)
unnamed: JP1.1 (A), U1.27 (DIAG1)
unnamed: JP1.3 (B), U1.26 (DIAG0)

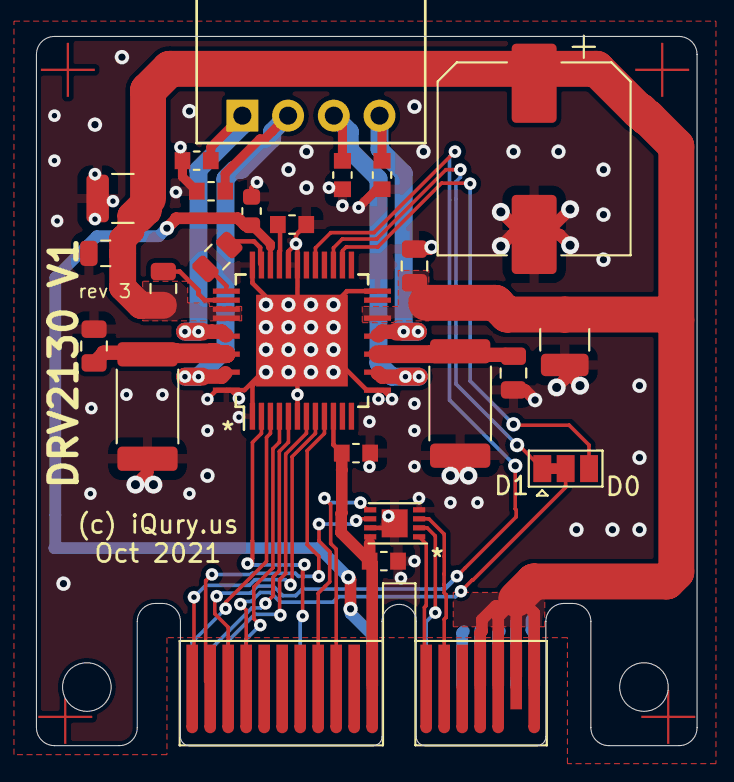
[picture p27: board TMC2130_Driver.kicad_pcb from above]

Board: 2 copper layers, 36.7 x 39.4 mm, 31 parts (1 on the bottom side), 30 nets.

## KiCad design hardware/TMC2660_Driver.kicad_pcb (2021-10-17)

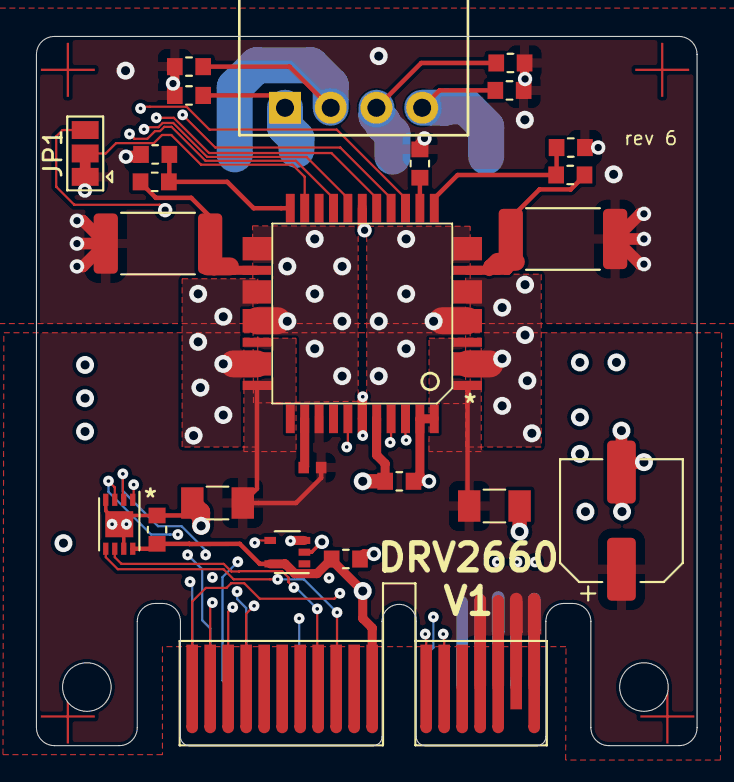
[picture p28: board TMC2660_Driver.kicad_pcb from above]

Board: 4 copper layers, 36.7 x 39.4 mm, 31 parts (1 on the bottom side), 29 nets.

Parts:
C1, C2: 10uF 50V; C_1206_3216Metric
C3, C6, C14: 0.1uF; C_0603_1608Metric
C4: 0.1uF 50V; C_0402_1005Metric
C5: 0.47uF; C_0603_1608Metric
C7, C12: 0.01uF; C_0603_1608Metric
C8, C9, C10, C11: 1000pF; C_0603_1608Metric
C13: 100uF 35V; CP_Elec_6.3x7.7
FID1, FID2, FID3, FID4: Fiducial; Fiducial_1mm_Dia_2.54mm_Outer_CopperTop
H1, H2: MountingHole; MountingHole_2.7mm_M2.5
J1: PCIe_Stepper; BUS_PCIexpress
J2: Conn_01x04_Male; Molex-SL-4POS
JP1: ClkIn; SolderJumper-3_P1.3mm_Bridged12_Pad1.0x1.5mm
LOGO1: Logo_Open_Hardware_Large; OSHW-Logo2_7.3x6mm_SilkScreen
R1, R3: 22R; R_0603_1608Metric
R2, R4: 0R051; R_2512_6332Metric
U1: TMC2660
U2: 74LVC1G06; SOT-353_SC-70-5
U3: 24LC02; TDFN-8-1EP_3x2mm_P0.5mm_EP1.56x1.45mm

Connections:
/ALARM1: J1.B4, U2.4
/CLOCK: J1.A7, JP1.3 (B)
/DIAG: U1.38 (SG_TST), U2.2
/DIR: J1.B2, U1.41 (DIR)
/ID_0: J1.B12, U3.1 (A0)
/ID_1: J1.A12, U3.2 (A1)
/ID_2: J1.B13, U3.3 (A2)
/MISO: J1.A3, U1.15 (SDI)
/MOSI: J1.A2, U1.14 (SDO)
/MOTA1: C8.2, J2.4, U1.2.3 (OA1), U1.7.8 (OA1)
/MOTA2: C9.2, J2.3, U1.5.6 (OA2), U1.10.1 (OA2)
/MOTB1: C10.2, J2.2, U1.26.7 (OB1), U1.31.2 (OB1)
/MOTB2: C11.2, J2.1, U1.23.4 (OB2), U1.28.9 (OB2)
/SCK: J1.A4, U1.16 (SCK)
/SCL: J1.B8, U3.6 (SCL)
/SDA: J1.B9, U3.5 (SDA)
/STEP: J1.B1, U1.42 (STEP)
/V_MOTORS: C1.1, C2.1, C4.1, C13.1, J1.B15, J1.B16, J1.B17, J1.B18, U1.1 (NC), U1.4 (VSA), U1.30 (VSB), U1.33 (NC), U1.36 (VS)
/~CS: J1.A1, U1.18 (~CS)
/~ENABLE: J1.B3, U1.19 (~EN)
GND: C1.2, C2.2, C3.2, C5.1, C6.2, C7.2, C8.1, C9.1, C10.1, C11.1, C12.2, C13.2, C14.2, J1.A14, J1.A15, J1.A16, J1.A17, J1.A18, JP1.1 (A), R2.2, R4.2, U1.17 (GND), U1.39 (GND), U1.43 (TST_MODE), U1.44 (GND), U2.3 (GND), U3.4 (GND), U3.7 (WP), U3.9 (PAD)
unnamed: C4.2, U1.35 (VHS)
unnamed: C5.2, U1.13 (5VOUT)
unnamed: C7.1, R1.1, U1.22 (SRB)
unnamed: C12.1, R3.1, U1.12 (SRA)
unnamed: R1.2, R2.1, U1.25 (BRB)
unnamed: R3.2, R4.1, U1.9 (BRA)
unnamed: JP1.2 (C), U1.21 (CLK)
VCC: C3.1, C6.1, C14.1, J1.B11, U1.40 (VCC_IO), U2.5 (VCC), U3.8 (VCC)

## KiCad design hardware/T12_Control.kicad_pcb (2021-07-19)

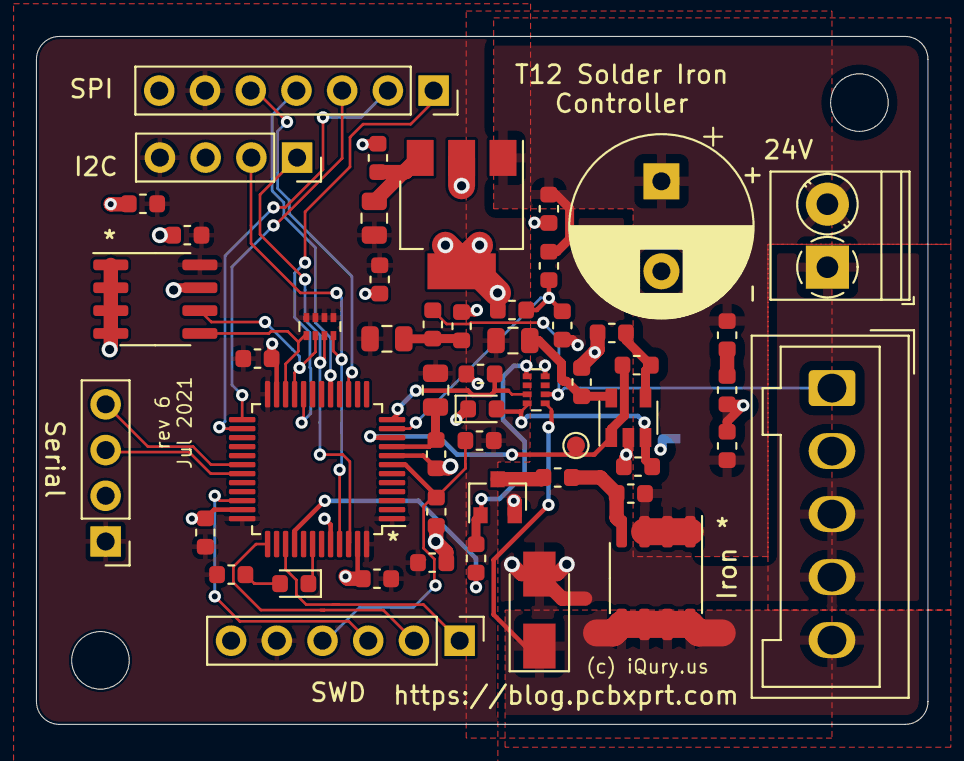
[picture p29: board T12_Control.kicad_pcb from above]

Board: 4 copper layers, 49.5 x 38.2 mm, 55 parts (1 on the bottom side), 37 nets.

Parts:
C1, C2, C3, C4, C6, C7, C8, C9, C11, C13, C14, C17: 100nF; C_0603_1608Metric
C5: 10uF; C_0603_1608Metric
C10, C18: 10nF; C_0603_1608Metric
C12: 100uF 35V; CP_Radial_D10.0mm_P5.00mm
C15: 1nF; C_0603_1608Metric
C16: 470pF; C_0603_1608Metric
C19: 1uF; C_0603_1608Metric
D1: RS1M; D_SMA
D2, D3: RED; LED_0603_1608Metric
FB1, FB2, FB3, FB4: Ferrite_Bead; L_0805_2012Metric
H1, H2: MountingHole; MountingHole_3.2mm_M3_DIN965
J1: Screw_Terminal_01x02; TerminalBlock_Phoenix_PT-1,5-2-3.5-H_1x02_P3.50mm_Horizontal
J2: GX12-5M; Wago_734-135_1x05_P3.50mm_Vertical
J3: SPI LCD; PinSocket_1x07_P2.54mm_Vertical
J4: I2C LCD; PinSocket_1x04_P2.54mm_Vertical
J5: SWD; PinHeader_1x06_P2.54mm_Vertical
J6: Serial; PinHeader_1x04_P2.54mm_Vertical
NT1: Net-Tie_2; NetTie-2_SMD_Pad0.5mm
Q1: TPC8107; SO-8_3.9x4.9mm_P1.27mm
Q2: BC817; SOT-23
R1: 2k; R_0603_1608Metric
R2, R7: 10k; R_0603_1608Metric
R3, R4, R9: 1k; R_0603_1608Metric
R5: 1k 0.1%; R_0603_1608Metric
R6: 249k 0.1%; R_0603_1608Metric
R8: 470; R_0603_1608Metric
R10: 2.2; R_0603_1608Metric
R11: 4.7k 1%; R_0603_1608Metric
RN1, RN2: 4x4.7k; R_Array_Concave_4x0402
TP1: TestPoint; TestPoint_Pad_D1.0mm
U1: SPX2954M3-3.3_SOT223; SOT-223-3_TabPin2
U2: 24LC32; SOIC-8_3.9x4.9mm_P1.27mm
U3: SGM8551XN; SOT-23-5
U4: STM32F103CBTx; LQFP-48_7x7mm_P0.5mm

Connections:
/3.3V: C3.1, C6.1, C7.1, C8.1, C9.1, C14.1, C17.1, FB1.2, FB2.1, FB3.1, FB4.1, J3.6, J4.4, J5.5, J6.1, R7.1, R9.2, RN2.1 (R1.1), RN2.2 (R2.1), RN2.3 (R3.1), RN2.4 (R4.1), U2.8 (VCC), U4.1 (VBAT), U4.24 (VDD), U4.36 (VDD), U4.48 (VDD)
/24V: C1.1, C2.1, C12.1, J1.2, Q1.1 (S), Q1.2 (S), Q1.3 (S), R1.1, R2.1, R10.1, U1.1 (VI)
/D/~C: J3.2, U4.26 (PB13)
/EE_SCL: RN2.6 (R3.2), U2.6 (SCL), U4.21 (PB10)
/EE_SDA: RN2.5 (R4.2), U2.5 (SDA), U4.22 (PB11)
/HEATER_ON: R8.2, U4.40 (PB4)
/MOSI: J3.4, U4.17 (PA7)
/NTC: C19.1, RN1.3 (R3.1), U4.12 (PA2)
/OLED_SCL: J4.2, RN2.8 (R1.2), U4.45 (PB8)
/OLED_SDA: J4.1, RN2.7 (R2.2), U4.46 (PB9)
/RX: J6.3, U4.31 (PA10)
/SCK: J3.5, U4.15 (PA5)
/SWDCLK: J5.2, U4.37 (PA14)
/SWDIO: J5.3, U4.34 (PA13)
/SWDSWO: J5.1, U4.39 (PB3)
/TIP_TEMP: R6.2, TP1.1, U3.1, U4.10 (PA0)
/TX: J6.4, U4.30 (PA9)
/V_MON: C4.1, R2.2, R4.1, U4.11 (PA1)
/~CS: J3.1, U4.20 (PB2)
/~NRST: C11.2, J5.4, R7.2, U4.7 (NRST)
/~RST: J3.3, U4.25 (PB12)
GND: C1.2, C2.2, C3.2, C4.2, C5.2, C6.2, C7.2, C8.2, C9.2, C11.1, C12.2, C14.2, C16.2, C17.2, C19.2, D1.2 (A), J1.1, J2.3, J2.4, J3.7, J4.3, J5.6, J6.2, NT1.2, Q2.2 (E), R4.2, RN1.8 (R1.2), U1.2 (GND), U2.1 (A0), U2.2 (A1), U2.3 (A2), U2.4 (GND), U2.7 (WP), U4.23 (VSS), U4.35 (VSS), U4.44 (BOOT0), U4.47 (VSS)
GNDA: C10.2, C13.2, C15.2, C18.2, D2.1 (K), NT1.1, R5.2, U3.2 (V-), U4.8 (VSSA)
unnamed: C5.1, FB1.1, U1.3 (VO)
unnamed: C10.1, FB2.2, U4.9 (VDDA)
unnamed: C13.1, FB3.2, U3.5 (V+)
unnamed: C15.1, D2.2 (A), RN1.4 (R4.1), U3.3 (+)
unnamed: C16.1, R10.2
unnamed: C18.1, FB4.2, R11.2
unnamed: D1.1 (K), J2.5, Q1.5 (D), Q1.6 (D), Q1.7 (D), Q1.8 (D), RN1.5 (R4.2)
unnamed: D3.1 (K), U4.42 (PB6)
unnamed: D3.2 (A), R9.1
unnamed: J2.1, R11.1, RN1.6 (R3.2)
unnamed: Q1.4 (G), R1.2, R3.1
unnamed: Q2.1 (B), R8.1, RN1.1 (R1.1)
unnamed: Q2.3 (C), R3.2
unnamed: R5.1, R6.1, U3.4 (-)

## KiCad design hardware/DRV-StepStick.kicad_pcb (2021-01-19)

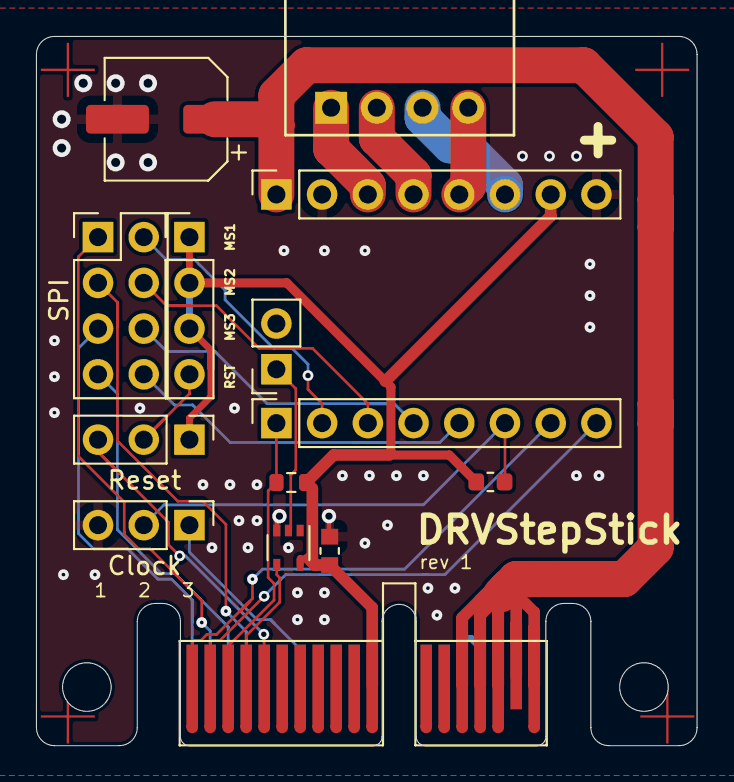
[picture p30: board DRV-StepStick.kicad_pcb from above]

Board: 2 copper layers, 36.7 x 39.4 mm, 21 parts (1 on the bottom side), 24 nets.

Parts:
C3: 0.1uF; C_0603_1608Metric
C4: 100uF 35V; CP_Elec_6.3x7.7
FID1, FID2, FID3, FID4: Fiducial; Fiducial_1mm_Dia_2.54mm_Outer_CopperTop
H1, H2: MountingHole; MountingHole_2.7mm_M2.5
J1: PCIe_Stepper; BUS_PCIexpress
J2: Motor; Molex-SL-4POS
J3: StepStickL; PinSocket_1x08_P2.54mm_Vertical
J4: StepStickR; PinSocket_1x08_P2.54mm_Vertical
J5: Conn_01x04; PinHeader_1x04_P2.54mm_Vertical
J6: SPI Mode; PinHeader_2x04_P2.54mm_Vertical
J7: Conn_01x02; PinSocket_1x02_P2.54mm_Vertical
JP3: Clock/Sleep; PinHeader_1x03_P2.54mm_Vertical
JP4: Reset; PinHeader_1x03_P2.54mm_Vertical
LOGO1: Logo_Open_Hardware_Large; OSHW-Logo2_7.3x6mm_SilkScreen
R1, R2: 10k; R_0603_1608Metric
U2: 74LVC1G06; SOT-353_SC-70-5

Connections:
/ALARM1: J1.B4, U2.4
/CLOCK: J1.A7, JP3.1 (A)
/DIAG: J7.1, U2.2
/DIR: J1.B2, J3.8
/MISO: J1.A3, J6.7
/MOSI: J1.A2, J6.1
/MOTA1: J2.4, J4.5
/MOTA2: J2.3, J4.6
/MOTB1: J2.2, J4.4
/MOTB2: J2.1, J4.3
/MS1/MOSI: J3.2, J6.2
/MS2/SCK: J3.3, J6.4
/MS3/~CS/UART: J3.4, J6.6
/RST/MISO/UART: J3.5, J6.8
/SCK: J1.A4, J6.3
/SLP/DCO/CLK/UART: J3.6, JP3.2 (C), R2.1
/STEP: J1.B1, J3.7
/VBB: C4.1, J1.B14, J1.B15, J1.B16, J1.B17, J1.B18, J4.1
/~CS: J1.A1, J6.5
/~ENABLE: J1.B3, J3.1, R1.2
/~ST_RESET: J1.B5, JP4.3 (B)
GND: C3.2, C4.2, J1.A14, J1.A15, J1.A16, J1.A17, J1.A18, J4.2, J4.8, JP3.3 (B), U2.3 (GND)
unnamed: J5.4, JP4.2 (C)
VCC: C3.1, J1.B11, J4.7, J5.1, J5.2, J5.3, JP4.1 (A), R1.1, R2.2, U2.5 (VCC)

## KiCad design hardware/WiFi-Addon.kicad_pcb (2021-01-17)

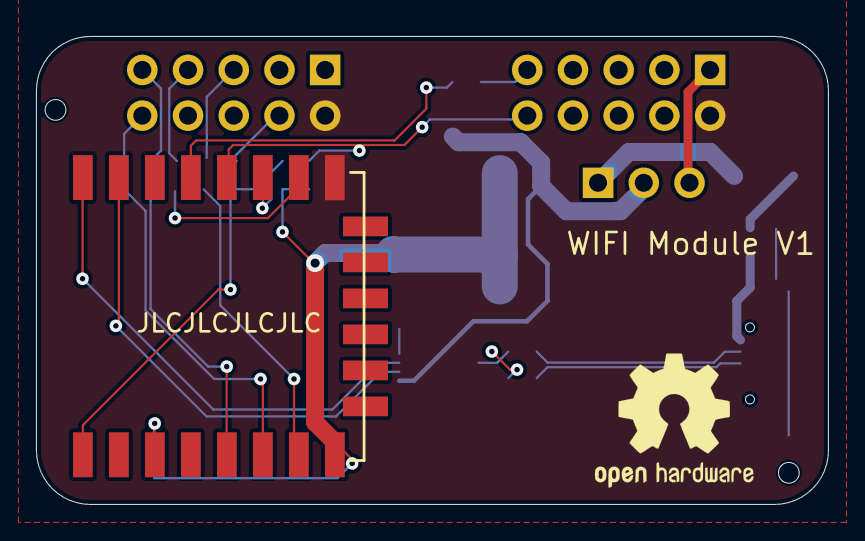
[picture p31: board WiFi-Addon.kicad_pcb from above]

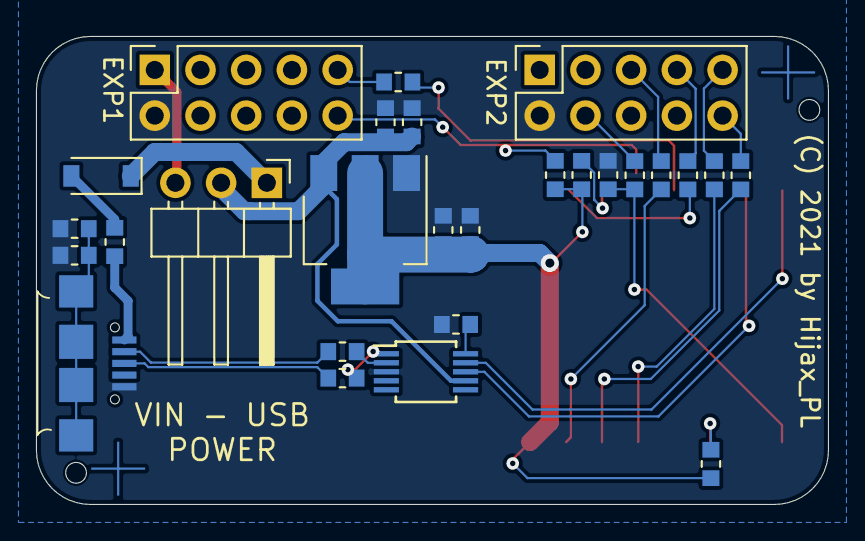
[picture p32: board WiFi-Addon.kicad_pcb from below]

Board: 2 copper layers, 44.0 x 26.0 mm, 33 parts (29 on the bottom side), 30 nets.

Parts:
C1, C4: 10uF; C_0603_1608Metric
C2, C3, C5, C19: 0.1uF; C_0603_1608Metric
C6: 10n; C_0603_1608Metric
D1: B5819W; D_SOD-123
EXP1, EXP2: IDC 2x5; PinSocket_2x05_P2.54mm_Vertical
F1: 500mA; R_0603_1608Metric
FID1, FID2: Fiducial; Fiducial_1mm_Dia_2.54mm_Outer_CopperTop
H1, H2: JLC Tooling Hole; JLC_Tool_hole
J1: PWR; PinHeader_1x03_P2.54mm_Horizontal
J3: USB_B_Micro; MC-101C
LOGO1: Logo_Open_Hardware_Small; OSHW-Logo2_9.8x8mm_SilkScreen
R1, R4, R6: 47R; R_0603_1608Metric
R2: 470R; R_0603_1608Metric
R3, R5: 2k2; R_0603_1608Metric
R7, R8, R13: 10k; R_0603_1608Metric
R10, R11: 22; R_0603_1608Metric
R12: 100k; R_0603_1608Metric
U1: AMS1117-3.3; SOT-223-3_TabPin2
U2: ESP-12F; ESP-12E_SMD
U3: CH340G; MSOP-10_3x3mm_P0.5mm

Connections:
3.3V: C3.1, C4.1, R7.2, R8.1, R13.1, U1.2 (VO), U2.8 (VCC)
5V: C1.1, C2.1, J1.2, U1.3 (VI), U3.7 (VCC)
/CSEL: EXP2.7, R5.1
/D+: J3.3 (D+), R11.1
/D-: J3.2 (D-), R10.1
/DATA_RDY: EXP1.10, R13.2, U2.12 (GPIO0)
/EN: R7.1, U2.3 (CH_PD)
/E_MISO: EXP2.10, R1.1
/E_MOSI: EXP2.5, R6.1
/E_RST: EXP2.4, R2.1
/E_SCK: EXP2.9, R4.1
/MISO: R1.2, U2.6 (GPIO12)
/MOSI: R6.2, U2.7 (GPIO13)
/RST: C5.2, R2.2, U2.1 (REST)
/SCK: R4.2, U2.5 (GPIO14)
/TRF_RDY: R3.2, U2.13 (GPIO4)
/VBUS: D1.1 (K), J1.1
/VIN: EXP1.1, J1.3
GND: C1.2, C2.2, C3.2, C4.2, C5.1, C6.1, C19.1, EXP1.2, EXP2.2, J3.5 (GND), R12.1, U1.1 (GND), U2.9 (GND), U3.3 (GND)
unnamed: C6.2, U3.10 (V3)
unnamed: C19.2, J3.6 (Shield), R12.2
unnamed: D1.2 (A), F1.2
unnamed: EXP1.9, R3.1
unnamed: F1.1, J3.1 (VBUS)
unnamed: R5.2, U2.10 (GPIO15)
unnamed: R8.2, U2.11 (GPIO2)
RX: U2.15 (RXD), U3.8 (TXD)
TX: U2.16 (TXD), U3.9 (RXD)
USB_D+: R11.2, U3.1 (UD+)
USB_D-: R10.2, U3.2 (UD-)

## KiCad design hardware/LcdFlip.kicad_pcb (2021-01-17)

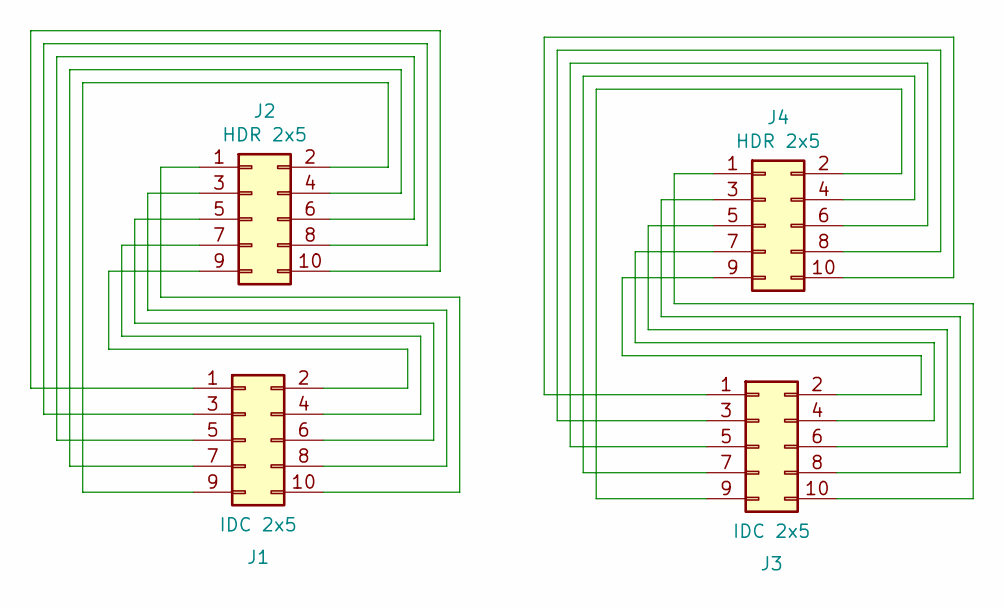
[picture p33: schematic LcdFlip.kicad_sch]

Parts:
J1, J3: IDC 2x5
J2, J4: HDR 2x5

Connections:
unnamed: J1.1, J2.10
unnamed: J1.2, J2.9
unnamed: J1.3, J2.8
unnamed: J1.4, J2.7
unnamed: J1.5, J2.6
unnamed: J1.6, J2.5
unnamed: J1.7, J2.4
unnamed: J1.8, J2.3
unnamed: J1.9, J2.2
unnamed: J1.10, J2.1
unnamed: J3.1, J4.10
unnamed: J3.2, J4.9
unnamed: J3.3, J4.8
unnamed: J3.4, J4.7
unnamed: J3.5, J4.6
unnamed: J3.6, J4.5
unnamed: J3.7, J4.4
unnamed: J3.8, J4.3
unnamed: J3.9, J4.2
unnamed: J3.10, J4.1

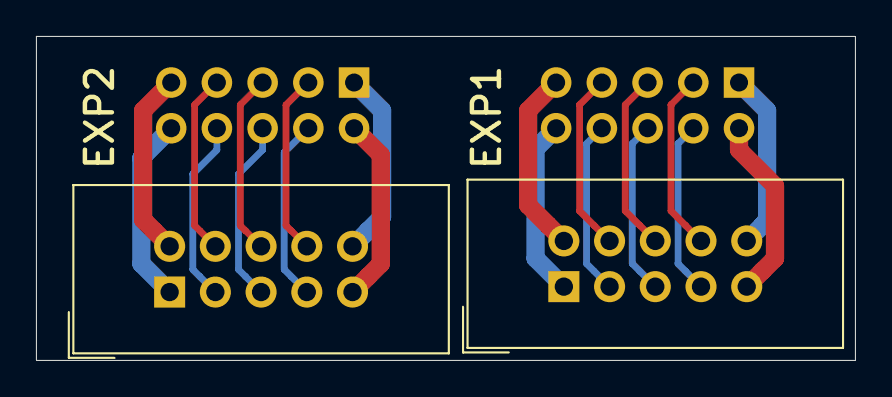
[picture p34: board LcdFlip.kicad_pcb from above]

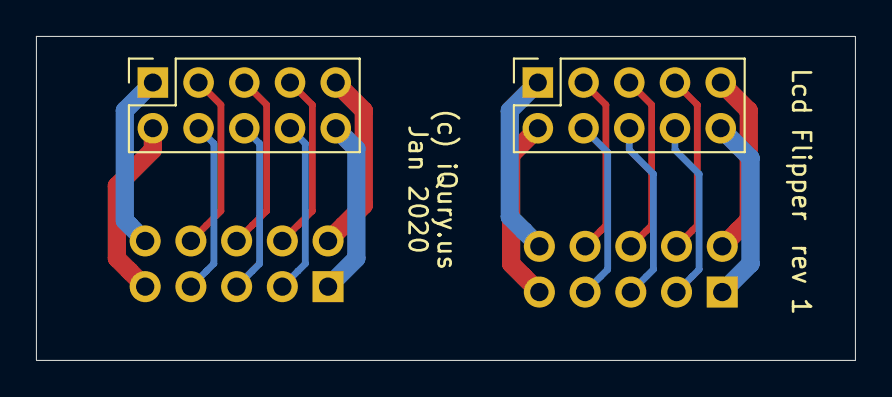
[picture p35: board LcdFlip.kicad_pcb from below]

Board: 2 copper layers, 45.5 x 18.0 mm, 4 parts (2 on the bottom side), 20 nets.

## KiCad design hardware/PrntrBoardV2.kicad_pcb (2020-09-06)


Board: 2 copper layers, 148.7 x 104.3 mm, 266 parts (0 on the bottom side), 177 nets.

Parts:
C1, C4, C7, C8, C9, C10, C11, C12, C13, C14, C17, C18, C19, C21, C22, C46, C53: 0.1uF; C_0603_1608Metric
C2, C5, C6, C15, C20, C23, C26: 10uF; C_0603_1608Metric
C3, C16, C27, C28, C29, C30, C31, C32, C33, C34, C35, C36, C37, C38, C39, C40, C45: 1000pF; C_0603_1608Metric
C24: 0.1uF 50V; C_0603_1608Metric
C25, C47, C48, C49, C50, C51, C52: 100uF 35V; CP_Elec_6.3x7.7
C41, C42, C43, C44: 10uF 50V; C_1206_3216Metric
D1: SS14; D_SMA
D2, D3, D4, D5, D13, D14, D15, D16, D17, D18, D19, D20, D23, D24, D28, D32: LED; LED_0603_1608Metric
D6: 10V; D_SOD-323
D7, D8, D9, D10, D11, D12: BAT54S; SOT-23
D22, D25, D26, D27, D29, D30, D31, D33, D34: 1N4148; D_SOD-323_HandSoldering
EXP1, EXP2, EXP3, EXP4: IDC 2x5; IDC-Header_2x05_P2.54mm_Vertical
F1: 500mA; R_0603_1608Metric
F2, F3, F4: Fuse; 2410_FuseFolder
FID1, FID2, FID3, FID4: Fiducial; Fiducial_1mm_Dia_2.54mm_Outer_CopperTop
H1, H2, H3, H4: MountingHole; MountingHole_3.2mm_M3
H5, H6, H7, H8: JLC Tooling Hole; JLC_Tool_hole
J1, J2, J4, J16, J18, J19, J21, J22, J23, J24, J25, J26, J27: JST XH; JST_XH_B2B-XH-A_1x02_P2.50mm_Vertical
J3: USB_B_Micro; MC-101C
J5: KF129; TerminalBlock_Phoenix_MKDS-1,5-2-5.08_1x02_P5.08mm_Horizont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
J6, J17, J20: KF350; TerminalBlock_Phoenix_PT-1,5-2-3.5-H_1x02_P3.50mm_Horizontal
J7, J8, J9, J10, J11, J12, J13, J14, J15: Conn_01x03_Male; PinHeader_1x03_P2.54mm_Vertical
JP1: Jumper_2_Open; PinHeader_1x02_P2.54mm_Vertical
JP2, JP3, JP4, JP5, JP6, JP7, JP8: Jumper_3_Open; PinHeader_1x03_P2.54mm_Vertical
J_SER1: Serial 0; PinHeader_1x04_P2.54mm_Vertical
J_ST1, J_ST2, J_ST3, J_ST4, J_ST5, J_ST6: PCIe_Stepper; AMPHENOL_10018784-10210TLF
J_SWD1: SWD; PinHeader_1x05_P2.54mm_Vertical
J_TH1, J_TH2, J_TH3, J_TH4, J_TH5, J_TH6: JST XH; JST_XH_B2B-XH-A_1x02_P2.50mm_Vertical
J_U-1: JST XH 3p; JST_XH_B3B-XH-A_1x03_P2.50mm_Vertical
J_V-1: JST XH 3p; JST_XH_B3B-XH-A_1x03_P2.50mm_Vertical
J_X+1: JST XH 3p; JST_XH_B3B-XH-A_1x03_P2.50mm_Vertical
J_X-1: JST XH 3p; JST_XH_B3B-XH-A_1x03_P2.50mm_Vertical
J_Y+1: JST XH 3p; JST_XH_B3B-XH-A_1x03_P2.50mm_Vertical
J_Y-1: JST XH 3p; JST_XH_B3B-XH-A_1x03_P2.50mm_Vertical
J_Z+1: JST XH 3p; JST_XH_B3B-XH-A_1x03_P2.50mm_Vertical
J_Z-1: JST XH 3p; JST_XH_B3B-XH-A_1x03_P2.50mm_Vertical
J_power_in1: KF635; TerminalBlock_MetzConnect_Type701_RT11L02HGLU_1x02_P6.35mm_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
LOGO1: Logo_Open_Hardware_Small; OSHW-Logo2_9.8x8mm_SilkScreen
Q1: NCE40P40K; TO-252-2
R1, R3, R5, R6, R7, R13, R14, R19, R20, R23, R24, R27, R28, R32, R33, R34, R38, R39, R40, R43, R44, R47, R48, R49, R50, R54, R55, R56, R58, R60, R61, R63, R64, R67, R68, R70: 10k; R_0603_1608Metric
R4: 1R5; R_0603_1608Metric
R8, R16, R29, R30, R31, R35, R36, R37, R41, R42, R51, R57, R62, R65, R69: 1k; R_0603_1608Metric
R9: 1.5k; R_0603_1608Metric
R10, R11: 22; R_0603_1608Metric
R12, R71: 100k; R_0603_1608Metric
R15, R45, R46: 470; R_0603_1608Metric
R17, R18, R21, R22, R25, R26: 4k7; R_0603_1608Metric
R52, R53, R59, R66: 180; R_0603_1608Metric
RN1, RN2: 4x470; R_Array_Convex_4x0603
RN3, RN4: 4x10k; R_Array_Convex_4x0603
SW_BOOT1: SW_Push; Button_4x4
SW_RST1: SW_Push; Button_4x4
TC1, TC2, TC3, TC4, TC5, TC6: TC; Molex-SL-6POS
TR1, TR4, TR6, TR7, TR9: SI2318CDS; SOT-23
TR2, TR3, TR5, TR8: PSMN7R0-30YL; SOT-669_LFPAK
U1, U7: 74LVC125; TSSOP-14_4.4x5mm_P0.65mm
U2: STM32F407VETx; LQFP-100_14x14mm_P0.5mm
U3: 24LC64; SO-8_3.9x4.9mm_P1.27mm
U4: AMS1117-3.3; SOT-223-3_TabPin2
U5: DCBuck; Buck2217
U6: 74HCT04; TSSOP-14_4.4x5mm_P0.65mm
X1: 12MHz; Oscillator_SMD_EuroQuartz_XO32-4Pin_3.2x2.5mm
XS1: MicroSD; Conn_uSDcard

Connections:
3.3V: C3.1, C4.1, C8.1, C9.1, C10.1, C11.1, C12.1, C13.1, C14.1, C15.1, C16.1, C17.1, C18.1, C22.1, C23.1, C53.1, EXP3.4, EXP4.2, J_ST1.B11, J_ST2.B11, J_ST2.B12, J_ST3.A12, J_ST3.B11, J_ST4.A12, J_ST4.B11, J_ST4.B12, J_ST5.B11, J_ST5.B13, J_ST6.B11, J_ST6.B12, J_ST6.B13, J_SWD1.2, R3.1, R4.1, R6.1, R7.1, R8.1, R9.2, R15.1, R29.1, R30.1, R31.1, R35.1, R36.1, R37.1, R41.1, R42.1, R47.1, R48.1, R49.1, R58.1, R63.1, R70.1, RN3.1 (R1.1), RN3.2 (R2.1), RN3.3 (R3.1), RN3.4 (R4.1), RN4.1 (R1.1), RN4.2 (R2.1), RN4.3 (R3.1), U1.14 (VCC), U2.6 (VBAT), U2.11 (VDD), U2.19 (VDD), U2.28 (VDD), U2.50 (VDD), U2.75 (VDD), U2.100 (VDD), U3.1 (A0), U3.2 (A1), U3.3 (A2), U3.8 (VCC), U4.2 (VO), U7.4, U7.5, U7.9, U7.10, U7.12, U7.13, U7.14 (VCC), X1.4 (V+), XS1.4 (Vdd)
5V: C20.1, C21.1, C26.1, C45.1, C46.1, D1.1 (K), EXP1.1, EXP3.2, EXP4.10, J1.1, J2.1, J7.2, J8.2, J9.2, J10.2, J11.2, J12.2, J13.2, J14.2, J15.2, J24.1, J25.1, JP2.1 (A), J_SER1.1, J_ST1.A11, J_ST2.A11, J_ST3.A11, J_ST4.A11, J_ST5.A11, J_ST6.A11, J_U-1.3, J_V-1.3, J_X+1.3, J_X-1.3, J_Y+1.3, J_Y-1.3, J_Z+1.3, J_Z-1.3, R16.1, TC1.2, TC2.2, TC3.2, TC4.2, TC5.2, TC6.2, U4.3 (VI), U5.5 (Vout), U5.6 (Vout), U6.14 (VCC)
/Sheet5DABBBAA/BOOT0: R1.1, SW_BOOT1.2, U2.94 (BOOT0)
/Sheet5DABBBAA/SPI1_MOSI_CPU: U1.9, U2.32 (PA7)
/Sheet5DABBBAA/SPI1_SCK_CPU: U1.5, U2.89 (PB3)
/Sheet5DABBBAA/SPI2_MOSI_CPU: U1.2, U2.18 (PC3)
/Sheet5DABBBAA/SPI2_SCK_CPU: U1.12, U2.52 (PB13)
/Sheet5DABBBAA/ST_RXTX_1: R46.2, U2.47 (PB10)
/Sheet5DABBBAA/ST_RXTX_2: R45.2, U2.63 (PC6)
/Sheet5DABBBAA/SWDCLK: J_SWD1.5, U2.76 (PA14)
/Sheet5DABBBAA/SWDIO: J_SWD1.4, U2.72 (PA13)
/Sheet5DAF0EF8/D+: J3.3 (D+), R9.1, R11.1
/Sheet5DAF0EF8/D-: J3.2 (D-), R10.1
/Sheet5DAF0EF8/E_BTN_ENC: EXP1.9, RN2.1 (R1.1)
/Sheet5DAF0EF8/E_ENC_A: EXP2.6, RN2.3 (R3.1)
/Sheet5DAF0EF8/E_ENC_B: EXP2.8, RN2.2 (R2.1)
/Sheet5DAF0EF8/E_LCD_D4: EXP1.6, RN1.1 (R1.1)
/Sheet5DAF0EF8/E_LCD_D5: EXP1.5, RN1.2 (R2.1)
/Sheet5DAF0EF8/E_LCD_D6: EXP1.4, RN1.3 (R3.1)
/Sheet5DAF0EF8/E_LCD_D7: EXP1.3, RN1.4 (R4.1)
/Sheet5DAF0EF8/E_MISO: EXP2.10, RN2.4 (R4.1)
ADC1: C27.1, D7.3 (common), R19.1, TC1.6, U2.23 (PA0)
ADC2: C29.1, D9.3 (common), R23.1, TC2.6, U2.24 (PA1)
ADC3: C31.1, D11.3 (common), R27.1, TC3.6, U2.25 (PA2)
ADC4: C28.1, D8.3 (common), R20.1, TC4.6, U2.26 (PA3)
ADC5: C30.1, D10.3 (common), R24.1, TC5.6, U2.29 (PA4)
ADC6: C32.1, D12.3 (common), R28.1, TC6.6, U2.30 (PA5)
AVREF: C6.1, C7.1, D7.2 (K), D8.2 (K), D9.2 (K), D10.2 (K), D11.2 (K), D12.2 (K), R4.2, R17.1, R18.1, R21.1, R22.1, R25.1, R26.1, U2.21 (VREF+), U2.22 (VDDA)
BEEP: EXP1.10, U2.48 (PB11)
BTN_ENC: RN2.8 (R1.2), U2.51 (PB12)
CLOCK: J_ST1.A7, J_ST2.A7, J_ST3.A7, J_ST4.A7, J_ST5.A7, J_ST6.A7, U2.12 (PH0), U7.3
ENC_A: RN2.6 (R3.2), U2.54 (PB15)
ENC_B: RN2.7 (R2.2), U2.53 (PB14)
GND: C1.2, C2.2, C3.2, C4.2, C5.2, C6.2, C7.2, C8.2, C9.2, C10.2, C11.2, C12.2, C13.2, C14.2, C15.2, C16.2, C17.2, C18.2, C19.1, C20.2, C21.2, C22.2, C23.2, C24.2, C25.2, C26.2, C27.2, C28.2, C29.2, C30.2, C31.2, C32.2, C33.2, C34.2, C35.2, C36.2, C37.2, C38.2, C39.2, C40.2, C41.2, C42.2, C43.2, C44.2, C45.2, C46.2, C47.2, C48.2, C49.2, C50.2, C51.2, C52.2, C53.2, D2.1 (K), D3.1 (K), D4.1 (K), D5.1 (K), D7.1 (A), D8.1 (A), D9.1 (A), D10.1 (A), D11.1 (A), D12.1 (A), EXP1.2, EXP2.2, EXP3.1, EXP4.1, J1.2, J2.2, J3.5 (GND), J7.3, J8.3, J9.3, J10.3, J11.3, J12.3, J13.3, J14.3, J15.3, J22.2, J23.2, J24.2, J25.2, J26.2, J27.2, J_SER1.2, J_ST1.A12, J_ST1.A13, J_ST1.A14, J_ST1.A15, J_ST1.A16, J_ST1.A17, J_ST1.A18, J_ST1.B12, J_ST1.B13, J_ST2.A12, J_ST2.A13, J_ST2.A14, J_ST2.A15, J_ST2.A16, J_ST2.A17, J_ST2.A18, J_ST2.B13, J_ST3.A13, J_ST3.A14, J_ST3.A15, J_ST3.A16, J_ST3.A17, J_ST3.A18, J_ST3.B12, J_ST3.B13, J_ST4.A13, J_ST4.A14, J_ST4.A15, J_ST4.A16, J_ST4.A17, J_ST4.A18, J_ST4.B13, J_ST5.A12, J_ST5.A13, J_ST5.A14, J_ST5.A15, J_ST5.A16, J_ST5.A17, J_ST5.A18, J_ST5.B12, J_ST6.A12, J_ST6.A13, J_ST6.A14, J_ST6.A15, J_ST6.A16, J_ST6.A17, J_ST6.A18, J_SWD1.1, J_TH1.2, J_TH2.2, J_TH3.2, J_TH4.2, J_TH5.2, J_TH6.2, J_U-1.2, J_V-1.2, J_X+1.2, J_X-1.2, J_Y+1.2, J_Y-1.2, J_Z+1.2, J_Z-1.2, J_power_in1.1, R1.2, R5.1, R12.1, R50.2, R56.2, R61.2, R64.2, R68.2, R71.2, SW_RST1.1, TC1.1, TC2.1, TC3.1, TC4.1, TC5.1, TC6.1, TR1.S, TR2.S, TR3.S, TR4.S, TR5.S, TR6.S, TR7.S, TR8.S, TR9.S, U1.1, U1.4, U1.7 (GND), U1.10, U1.13, U2.10 (VSS), U2.20 (VSSA), U2.27 (VSS), U2.74 (VSS), U2.99 (VSS), U3.4 (GND), U3.7 (WP), U4.1 (GND), U5.3 (GND), U5.4 (GND), U5.7 (GND), U5.8 (GND), U6.5, U6.7 (GND), U6.9, U7.1, U7.7 (GND), X1.2 (GND), XS1.6 (GND)
I2C_SCL: EXP3.10, J_ST1.B8, J_ST2.B8, J_ST3.B8, J_ST4.B8, J_ST5.B8, J_ST6.B8, R6.2, U2.92 (PB6), U3.6 (SCL)
I2C_SDA: EXP3.8, J_ST1.B9, J_ST2.B9, J_ST3.B9, J_ST4.B9, J_ST5.B9, J_ST6.B9, R7.2, U2.93 (PB7), U3.5 (SDA)
LCD_D4: RN1.8 (R1.2), U2.46 (PE15)
LCD_D5: RN1.7 (R2.2), U2.45 (PE14)
LCD_D6: RN1.6 (R3.2), U2.44 (PE13)
LCD_D7: RN1.5 (R4.2), U2.43 (PE12)
LCD_RS: EXP1.7, U2.42 (PE11)
unnamed: C2.1, U2.49 (VCAP_1)
unnamed: C5.1, U2.73 (VCAP_2)
unnamed: C19.2, J3.6 (Shield), R12.2
unnamed: C33.1, D13.1 (K), J_X-1.1, R32.2
unnamed: C34.1, D14.1 (K), J_X+1.1, R33.2
unnamed: C35.1, D15.1 (K), J_U-1.1, R34.2
unnamed: C36.1, D16.1 (K), J_Y-1.1, R38.2
unnamed: C37.1, D17.1 (K), J_Y+1.1, R39.2
unnamed: C38.1, D18.1 (K), J_V-1.1, R40.2
unnamed: C39.1, D19.1 (K), J_Z-1.1, R43.2
unnamed: C40.1, D20.1 (K), J_Z+1.1, R44.2
unnamed: D1.2 (A), F1.2
unnamed: D2.2 (A), R13.2
unnamed: D3.2 (A), R14.2
unnamed: D4.2 (A), R15.2
unnamed: D5.2 (A), R16.2
unnamed: D6.2 (A), Q1.1 (G), R71.1
unnamed: D13.2 (A), R29.2
unnamed: D14.2 (A), R30.2
unnamed: D15.2 (A), R31.2
unnamed: D16.2 (A), R35.2
unnamed: D17.2 (A), R36.2
unnamed: D18.2 (A), R37.2
unnamed: D19.2 (A), R41.2
unnamed: D20.2 (A), R42.2
unnamed: D22.2 (A), J4.2, TR1.D
unnamed: D23.1 (K), D25.2 (A), J5.2, TR2.D
unnamed: D23.2 (A), R54.2
unnamed: D24.1 (K), D26.2 (A), J6.2, TR3.D
unnamed: D24.2 (A), R55.2
unnamed: D27.2 (A), J16.2, TR4.D
unnamed: D28.1 (K), D29.2 (A), J17.2, TR5.D
unnamed: D28.2 (A), R60.2
unnamed: D30.2 (A), J18.2, TR6.D
unnamed: D31.2 (A), J19.2, TR7.D
unnamed: D32.1 (K), D33.2 (A), J20.2, TR8.D
unnamed: D32.2 (A), R67.2
unnamed: D34.2 (A), J21.2, TR9.D
unnamed: EXP2.1, JP1.2 (B)
unnamed: F1.1, J3.1 (VBUS)
unnamed: F2.1, F3.1, F4.1, J_power_in1.2
unnamed: F4.2, Q1.2 (D)
unnamed: J_TH1.1, R17.2, R19.2
unnamed: J_TH2.1, R21.2, R23.2
unnamed: J_TH3.1, R25.2, R27.2
unnamed: J_TH4.1, R18.2, R20.2
unnamed: J_TH5.1, R22.2, R24.2
unnamed: J_TH6.1, R26.2, R28.2
unnamed: R8.2, SW_BOOT1.1
unnamed: R51.1, TR1.G
unnamed: R52.1, TR2.G
unnamed: R52.2, U6.2
unnamed: R53.1, TR3.G
unnamed: R53.2, U6.12
unnamed: R57.1, TR4.G
unnamed: R59.1, TR5.G
unnamed: R59.2, U6.4
unnamed: R62.1, TR6.G
unnamed: R65.1, TR7.G
unnamed: R66.1, TR8.G
unnamed: R66.2, U6.10
unnamed: R69.1, TR9.G
unnamed: RN4.5 (R4.2), RN4.6 (R3.2), XS1.9 (CD)
unnamed: U7.2, X1.3 (OUT)
PWM1: J7.1, R48.2, U2.67 (PA8), U6.1
PWM2: J10.1, R58.2, U2.77 (PA15), U6.3
PWM3: J13.1, R63.2, U2.90 (PB4), U6.11
PWM4: J8.1, R49.2, U2.95 (PB8), U6.13
PWM5: J11.1, R56.1, R57.2, U2.96 (PB9)
PWM6: J14.1, R61.1, R62.2, U2.64 (PC7)
PWM7: J9.1, R64.1, R65.2, U2.4 (PE5)
PWM8: J12.1, R68.1, R69.2, U2.5 (PE6)
PWM9: J15.1, R50.1, R51.2, U2.62 (PD15)
SDIO_CLK: EXP4.8, RN3.5 (R4.2), U2.80 (PC12), XS1.5 (CLK)
SDIO_CMD: EXP4.7, RN3.6 (R3.2), U2.83 (PD2), XS1.3 (DI/CMD)
SDIO_D0: EXP4.3, RN4.8 (R1.2), U2.65 (PC8), XS1.7 (DO/DAT0)
SDIO_D1: EXP4.4, RN4.7 (R2.2), U2.66 (PC9), XS1.8 (DAT1)
SDIO_D2: EXP4.5, RN3.8 (R1.2), U2.78 (PC10), XS1.1 (DAT2)
SDIO_D3: EXP4.6, RN3.7 (R2.2), U2.79 (PC11), XS1.2 (CS/DAT3)
SPI1_MISO: J_ST1.A2, J_ST2.A2, J_ST3.A2, J_ST4.A2, J_ST5.A2, J_ST6.A2, TC1.5, TC2.5, TC3.5, TC4.5, TC5.5, TC6.5, U2.31 (PA6)
SPI1_MOSI: J_ST1.A3, J_ST2.A3, J_ST3.A3, J_ST4.A3, J_ST5.A3, J_ST6.A3, TC1.4, TC2.4, TC3.4, TC4.4, TC5.4, TC6.4, U1.8
SPI1_SCK: J_ST1.A4, J_ST2.A4, J_ST3.A4, J_ST4.A4, J_ST5.A4, J_ST6.A4, TC1.3, TC2.3, TC3.3, TC4.3, TC5.3, TC6.3, U1.6
SPI2_MISO: RN2.5 (R4.2), U2.17 (PC2)
SPI2_MOSI: EXP2.5, U1.3
SPI2_SCK: EXP2.9, U1.11
ST1_DIR: J_ST1.B2, U2.61 (PD14)
ST1_STEP: J_ST1.B1, U2.97 (PE0)
ST2_DIR: J_ST2.B2, U2.60 (PD13)
ST2_STEP: J_ST2.B1, U2.91 (PB5)
ST3_DIR: J_ST3.B2, U2.59 (PD12)
ST3_STEP: J_ST3.B1, U2.88 (PD7)
ST4_DIR: J_ST4.B2, U2.58 (PD11)
ST4_STEP: J_ST4.B1, U2.85 (PD4)
ST5_DIR: J_ST5.B2, U2.57 (PD10)
ST5_STEP: J_ST5.B1, U2.82 (PD1)
ST6_DIR: J_ST6.B2, U2.56 (PD9)
ST6_STEP: J_ST6.B1, U2.81 (PD0)
ST_UART1: J_ST1.A6, J_ST2.A6, J_ST3.A6, J_ST4.A6, R46.1
ST_UART2: J_ST5.A6, J_ST6.A6, R45.1
UART2_RX: EXP3.7, U2.87 (PD6)
UART2_TX: EXP3.9, U2.86 (PD5)
UART_RX: EXP3.3, J_SER1.3, U2.69 (PA10)
UART_TX: EXP3.5, J_SER1.4, U2.68 (PA9)
USB_D+: R11.2, U2.71 (PA12)
USB_D-: R10.2, U2.70 (PA11)
V_bed: C41.1, D25.1 (K), F2.2, J5.1, R54.1
V_fan: D22.1 (K), D27.1 (K), D30.1 (K), D31.1 (K), D34.1 (K), J4.1, J16.1, J18.1, J19.1, J21.1, JP2.2 (C), R13.1
V_heaters: C42.1, C43.1, C44.1, D26.1 (K), D29.1 (K), D33.1 (K), F3.2, J6.1, J17.1, J20.1, R55.1, R60.1, R67.1
V_motors: C24.1, C25.1, C47.1, C48.1, C49.1, C50.1, C51.1, C52.1, D6.1 (K), J22.1, J23.1, J26.1, J27.1, JP2.3 (B), J_ST1.B14, J_ST1.B15, J_ST1.B16, J_ST1.B17, J_ST1.B18, J_ST2.B14, J_ST2.B15, J_ST2.B16, J_ST2.B17, J_ST2.B18, J_ST3.B14, J_ST3.B15, J_ST3.B16, J_ST3.B17, J_ST3.B18, J_ST4.B14, J_ST4.B15, J_ST4.B16, J_ST4.B17, J_ST4.B18, J_ST5.B14, J_ST5.B15, J_ST5.B16, J_ST5.B17, J_ST5.B18, J_ST6.B14, J_ST6.B15, J_ST6.B16, J_ST6.B17, J_ST6.B18, Q1.3 (S), R14.1, U5.1 (Vin), U5.2 (Vin)
~ALARM1: JP3.1 (A), JP4.1 (A), JP5.1 (A), JP6.1 (A), JP7.1 (A), JP8.1 (A), R47.2, U2.9 (PC15)
~EXP_CS: EXP3.6, JP1.1 (A), U2.55 (PD8)
~LCD_E: EXP1.8, U2.41 (PE10)
~RESET: C1.1, EXP2.3, J_SWD1.3, R3.2, SW_RST1.2, U2.14 (NRST)
~SD_DETECT: EXP2.7, EXP4.9, RN4.4 (R4.1), U2.84 (PD3)
~ST1_ALARM: JP3.2 (C), J_ST1.B4
~ST1_CS: J_ST1.A1, R5.2, U2.37 (PB2)
~ST2_ALARM: JP5.2 (C), J_ST2.B4
~ST2_CS: J_ST2.A1, U2.7 (PC13)
~ST3_ALARM: JP8.2 (C), J_ST3.B4
~ST3_CS: J_ST3.A1, U2.3 (PE4)
~ST4_ALARM: JP4.2 (C), J_ST4.B4
~ST4_CS: J_ST4.A1, U2.2 (PE3)
~ST5_ALARM: JP6.2 (C), J_ST5.B4
~ST5_CS: J_ST5.A1, U2.1 (PE2)
~ST6_ALARM: JP7.2 (C), J_ST6.B4
~ST6_CS: J_ST6.A1, U2.98 (PE1)
~ST_ENABLE: J_ST1.B3, J_ST2.B3, J_ST3.B3, J_ST4.B3, J_ST5.B3, J_ST6.B3, R70.2, U2.15 (PC0)
~ST_RESET: J_ST1.B5, J_ST2.B5, J_ST3.B5, J_ST4.B5, J_ST5.B5, J_ST6.B5, U2.16 (PC1)
~U_MIN: JP4.3 (B), R34.1, U2.39 (PE8)
~V_MIN: JP6.3 (B), R40.1, U2.40 (PE9)
~X_MAX: R33.1, U2.36 (PB1)
~X_MIN: JP3.3 (B), R32.1, U2.33 (PC4)
~Y_MAX: R39.1, U2.8 (PC14)
~Y_MIN: JP5.3 (B), R38.1, U2.34 (PC5)
~Z_MAX: JP7.3 (B), R44.1, U2.38 (PE7)
~Z_MIN: JP8.3 (B), R43.1, U2.35 (PB0)

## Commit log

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2019-09-30 Move all hardware design files to the hardware folder.
    [TMC2660_Driver.kicad_pcb, TMC2660_Driver.sch]
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2019-10-02 Routed TMC2660 driver in the new pluggable form factor.
    [TMC2660_Driver-B_Cu.gbl, TMC2660_Driver-B_Mask.gbs, TMC2660_Driver-B_Paste.gbp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]
2019-10-03 Adjust power traces width to match the pins. Updated to rev2.
    [TMC2660_Driver-B_Cu.gbl, TMC2660_Driver-B_Mask.gbs, TMC2660_Driver-B_Paste.gbp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]
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2019-10-20 Re-organized schematics into hierarchical sheets. Added ADC inputs.
    [Adc.sch, IO_Connectors.sch, Power.sch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]
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2019-10-20 Fix annotations for U6 parts.
    [Pwm.sch]
2019-10-20 Remove extra labels from the stepper driver wires.
    [DriverConnectors.sch]
2019-10-20 Fix some global name mistakes.
    [Adc.sch, Endstops.sch, Power.sch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]
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2019-10-20 Fix foorprint library name.
    [Adc.sch, Endstops.sch, IO_Connectors.sch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]
2019-10-21 Update 3D models for components. Switch thermistors to JST connectors.
    [PrntrBoardV2.kicad_pcb, Pwm.sch]
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2019-10-21 Placed more RC components next to the respective connectors.
    [Power.sch, PrntrBoardV2.kicad_pcb]
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2019-10-21 Adde mounting holes to the PCIe connectors. Hide all references.
    [PrntrBoardV2.kicad_pcb]
2019-10-22 Move driver holes a bit. Fix OSHW logo to appear.
    [PrntrBoardV2.kicad_pcb, PrntrBoardV2.sch, TMC2209_Driver.kicad_pcb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]
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2019-10-26 65 tracks to go. Fixed DRC issues.
    [PrntrBoardV2.kicad_pcb]
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2019-10-27 What is more embarasin than a typo on the silk screen?
    [PrntrBoardV2.kicad_pcb]
2019-10-27 Update the gerber files with the fixed typo.
    [PrntrBoardV2-B_Cu.gbl, PrntrBoardV2-B_Mask.gbs, PrntrBoardV2-B_Paste.gbp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]
2019-10-27 Fix 5V fan location.
    [PrntrBoardV2-B_Cu.gbl, PrntrBoardV2-B_Mask.gbs, PrntrBoardV2-B_Paste.gbp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]
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2019-10-29 Fix component values.
    [Adc.sch, DriverConnectors.sch, Endstops.sch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]
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2019-10-31 Added silk screen for Fuse values. Moved labels around.
    [PrntrBoardV2.kicad_pcb]
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2019-11-04 Replace 74HCT02 with 74HCT04.
    [PrntrBoardV2.kicad_pcb, Pwm.sch]
2019-11-06 Flip endstop signals to match RAMPS variants.
    [Endstops.sch, PrntrBoardV2.kicad_pcb]
2019-11-06 Swap the location of EXT1 and EXT2 to match the RAMPS placement.
    [PrntrBoardV2.kicad_pcb]
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2019-11-06 Update the current sense resistors on the 2660 driver to 2532 size.
    [TMC2660_Driver.kicad_pcb, TMC2660_Driver.sch]
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2019-11-09 Update footprints so the center is at 0,0
    [PrntrBoardV2.kicad_pcb]
2019-11-09 Update 3d model path and adjust offset to match the footprints.
    [PrntrBoardV2.kicad_pcb]
2019-11-10 Fix more 3D foorprint paths.
    [PrntrBoardV2.kicad_pcb, TMC2209_Driver.kicad_pcb]
2019-11-10 Update all 3d foorptints to point to the local project folder.
    [PrntrBoardV2.kicad_pcb]
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2019-11-11 Add I2C EEPROM to the 2209 driver board for identification.
    [PrntrBoardV2.kicad_pcb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]
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2019-11-12 Add metadata for the rest fo the components.
    [Adc.sch, Endstops.sch, IO_Connectors.sch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]
2019-11-12 Add metadata for missed resistor values.
    [IO_Connectors.sch, Power.sch, Pwm.sch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]
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2019-11-17 Update QFN footprint to match the Trinamic spec.
    [TMC2209_Driver-B_Cu.gbl, TMC2209_Driver-B_Mask.gbs, TMC2209_Driver-B_Paste.gbp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]
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2019-11-22 Fix design rules for the 2208 driver. Update EEPROM foorprint.
    [TMC2209_Driver-B_Cu.gbl, TMC2209_Driver-B_Mask.gbs, TMC2209_Driver-B_Paste.gbp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]
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2019-11-25 Swap EXP2 & EXP1 locations again.
    [PrntrBoardV2.kicad_pcb]
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2019-11-26 Update buck convertor footprint, so check if the new MP module would fit the board profile.
    [MP-Power.kicad_pcb, Power.sch, PrntrBoardV2.kicad_pcb]
2019-11-26 Fix layer on solder pad oppenings.
    [MP-Power.kicad_pcb, XL-Power.kicad_pcb]
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2019-11-30 Fix broken text labels.
    [PrntrBoardV2.kicad_pcb]
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2019-12-02 Change the ST_ENABLE to pull up as it is active low.
    [PrntrBoardV2.kicad_pcb, mcu.sch]
2019-12-02 Fix D21, it had incorrect foorprint.
    [Power.sch, PrntrBoardV2.kicad_pcb]
2019-12-07 Re-route USB data lines, the diff pair was damaged after adding EXP4.
    [PrntrBoardV2.kicad_pcb]
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2019-12-08 Add schematics for the drivers in teh doc/ folder.
    [TMC2209_Driver.sch, TMC2660_Driver.sch]
2019-12-08 Updated reverse voltage protection.
    [Adc.sch, DriverConnectors.sch, Endstops.sch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]
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2019-12-12 Route one missed trace.
    [MP-Power.kicad_pcb]
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2019-12-24 Update libraries to match the latest Windows release. Fix DRC issues.
    [MP-Power.kicad_pcb, PrntrBoardV2.kicad_pcb, Pwm.sch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]
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2020-03-01 Fix label positions.
    [TMC2660_Driver.kicad_pcb, TMC2660_Driver.sch]
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2020-03-02 Remove the mounting holes from the 2209 driver. SHould be used on a panel.
    [TMC2209_Driver.kicad_pcb, TMC2209_Driver.sch]
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2020-03-10 Fix DRC warnings. Update U3 metadata.
    [TMC2130_Driver-B_Cu.gbl, TMC2130_Driver-B_Mask.gbs, TMC2130_Driver-B_Paste.gbp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]
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2020-05-03 Switch sense resistors to 2512 and values to 0.12 Ohm to increase max current to 1.64A RMS.
    [TMC2130_Driver.kicad_pcb, TMC2130_Driver.sch]
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2020-05-03 Move some NC designators on the schematics so they touch the pins.
    [TMC2130_Driver.kicad_pcb, TMC2130_Driver.sch]
2020-05-04 Added external clock source and routed it to the Stepper. Make the TMC2130 use the external clock.
    [Adc.sch, DriverConnectors.sch, Endstops.sch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]
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2020-06-21 Fix all DRC issues. All traces routed.
    [PrntrBoardV2.kicad_pcb]
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2020-10-08 Update to the latest daily Kicad. Fix board outline issue on PrntrBoardV2.
    [TMC2130_Driver.kicad_pcb, TMC2209_Driver.kicad_pcb, TMC2660_Driver.kicad_pcb]
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2020-11-01 Updated DRC rules. Fix labels.
    [TMC2130_Driver.kicad_pcb, TMC2209_Driver.kicad_pcb, TMC2660_Driver.kicad_pcb]
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2020-11-14 Fix edge file name.
    [T12_Control-Edge_Cuts.gko]
2020-11-14 Revert the resistor networks back to 4x0402 footprint, not using JLC assembly svc for now.
    [T12_Control-B_Cu.gbl, T12_Control-B_Mask.gbs, T12_Control-B_Silkscreen.gbo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]
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2020-11-19 Do length matching on the SD-card lines, to prevent issues with 4b SDIO mode.
    [DriverConnectors.kicad_sch, IO_Connectors.kicad_sch, mcu.kicad_sch]
2020-11-19 Revert "Do length matching on the SD-card lines, to prevent issues with 4b SDIO mode."
    This reverts commit da3406b2e34481ff4c80c4903b4a4e071462965b.
    [DriverConnectors.kicad_sch, IO_Connectors.kicad_sch, mcu.kicad_sch]
2020-12-02 Add more input protection. 480 ohm resistors on all direct IO pins. Clamping diodes on the endstops.
    [Adc.kicad_sch, DriverConnectors.kicad_sch, Endstops.kicad_sch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]
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2020-12-02 Revert "Add new components to schematics."
    This reverts commit e0f79db81af6fe36e82911e577343ca8b29a9e90.
    [Adc.kicad_sch, DriverConnectors.kicad_sch, IO_Connectors.kicad_sch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]
2020-12-02 Revert "Add more input protection. 480 ohm resistors on all direct IO pins."
    This reverts commit 49fdbd5165b8c1709549cdf3235e4b40c9a44330.
    [Adc.kicad_sch, DriverConnectors.kicad_sch, Endstops.kicad_sch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]
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2020-12-20 Update the 1N4148 diodes to B5819W. The 1N was too puny to serve as protection.
    [Adc.kicad_sch, DriverConnectors.kicad_sch, Endstops.kicad_sch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]
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2021-01-03 Update to rev 5. Add jumper to select USB powering the board or not.
    [DriverConnectors.kicad_sch, IO_Connectors.kicad_sch, PrntrBoardV2.kicad_sch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]
2021-01-15 5V terminal added
    - dedicated input of 5V to allow control of external 24V supply
    - minotr tracks adjustment / cleaning
    [DriverConnectors.kicad_sch, Power.kicad_sch, PrntrBoardV2.kicad_sch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]
2021-01-16 Added CAN
    - Added CAN interface (PD0-1) with RJ 6p6c terminal
    - SD card moved to back /left side and switched to SPI mode
    - removed EXP4 headrr
    [DriverConnectors.kicad_sch, IO_Connectors.kicad_sch, PrntrBoardV2.kicad_sch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]
2021-01-16 Fix DRC violation.
    [DriverConnectors.kicad_sch, IO_Connectors.kicad_sch, mcu.kicad_sch]
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2021-01-17 Correcting footprint, and adding manufacturing markers
    Gerber files & interactive BOM generated
    [WiFi-Addon-B_Cu.gbl, WiFi-Addon-B_Mask.gbs, WiFi-Addon-B_Paste.gbp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]
2021-01-17 Add old LCD flipper add-on.
    [LcdFlip.kicad_pcb, LcdFlip.sch]
2021-01-17 Correction of header placement
    Proper layer and spacing.
    Plus small jumper to select USB or VIN power for WIFi
    [WiFi-Addon-B_Cu.gbl, WiFi-Addon-B_Mask.gbs, WiFi-Addon-B_Paste.gbp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]
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2021-01-17 Added some more information to schema
    Added datasheet links to ESP-12F and ESP8266EX
    Some additional info on schematics and repositioning of resistors for better understed of their purpose.
    [WiFi-Addon-B_Cu.gbl, WiFi-Addon-B_Mask.gbs, WiFi-Addon-B_Paste.gbp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]
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2021-01-18 Update the StepStick driver schematics, revert the routing.
    [DRV-StepStick.kicad_pcb, DRV-StepStick.kicad_sch]
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2021-01-18 Small pcb corections
    - populated GND vias around the pcb
    - updated copyright info
    [DRV-StepStick-B_Cu.gbl, DRV-StepStick-B_Mask.gbs, DRV-StepStick-B_Paste.gbp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]
2021-01-18 Update StepStick manufactirung files. Change copper zones with thermal relief. Added manufacturing scripts.
    [DRV-StepStick-BOM-jlc.csv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]
2021-01-18 Wire sd-card to SPI1, add sd_card_ss (~SD_CS) pin. Add EXP_CD pin for EXP2.4. Add dedicated EXP_SS pin for EXP2.7 - no longer has to share ~SD_DETECT. Added new pin ~EXP_CS2, replaced 3.3V supply on 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
    Removed 3.3V power supply from extension header. The 3.3V power supply is
    very limited (500mA) and we need it clean for the ADCs to work well.
    [IO_Connectors.kicad_sch, mcu.kicad_sch]
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2021-01-18 Add missing pull up resistor from sd-card.
    [IO_Connectors.kicad_sch, PrntrBoardV2.kicad_sch]
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2021-01-30 Rotate the display connectors 180 degrees. Add extra filter cap on pin 1 (VBAT). Improve PCB layout.
    [T12_Control.kicad_pcb, T12_Control.kicad_sch]
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2021-08-14 Convert SCH files to latest version. Fix DRC Warnings in PrntrBoard.
    [Adc.kicad_sch, DriverConnectors.kicad_sch, Endstops.kicad_sch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]
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2021-08-26 Improve ADC ground: add separate GNDA bus; add ferrite bead to AVREF power.
    [Adc.kicad_sch, PrntrBoardV2.kicad_sch, mcu.kicad_sch]
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2021-10-16 Added separate power supply for motor drivers, to accomodate high voltage driver versions.
    [Adc.kicad_sch, DriverConnectors.kicad_sch, IO_Connectors.kicad_sch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]
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

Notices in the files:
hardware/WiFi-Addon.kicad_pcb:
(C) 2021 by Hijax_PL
